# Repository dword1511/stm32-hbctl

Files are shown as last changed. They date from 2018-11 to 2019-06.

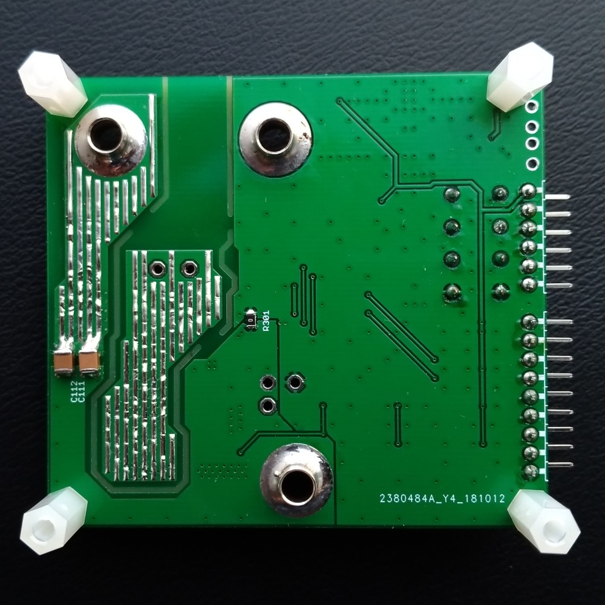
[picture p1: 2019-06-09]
pcb/pcb-photo-back.jpg

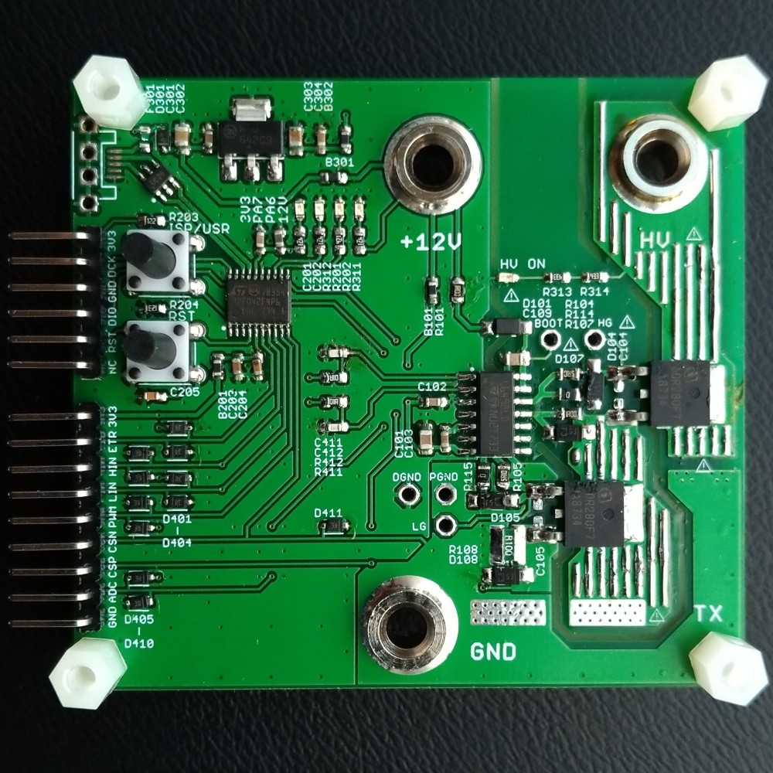
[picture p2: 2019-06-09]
pcb/pcb-photo-front.jpg

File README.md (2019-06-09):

# STM32-based half-bridge controller

This firmware code uses an `STM32F042` MCU to generate waveform for a STMicro `L6498` half-bridge driver,
which drives the MOSFETs in the inverter.

This particular inverter delivers 1 MHz AC current for our capacitive power transfer (CPT) project.
It has onboard buttons allowing us to cycle through 1 MHz +/- 100 kHz, with a few kHz of resolution.
It also has USB for ISP/DFU.

Unusual things this firmware does:

* Using HSI48 trimming in conjunction with timer prescaler to deliver a resolution of a few kHz across a large frequency range.
* Using a generic timer (rather than the advanced one) to generate complementary waveforms with dead time.

## General Build Instructions

You will need the following packages (Debian/Ubuntu):

* build-essential
* gcc-arm-none-eabi
* git
* dfu-util

The firmware can be loaded via USB DFU. However, you can also flash and debug via SWD. To do so, install the following package:

* stlink-tools
* gdb-multiarch

This project uses `libopencm3`. It will be automatically checked out during the building process.
To build the firmware, run `make`. To flash it, hold the `ISP/USR` button on the board, connect the board to USB, and then run `make flash-dfu`.

## Special Directions for CPT

Please be aware of the high voltage, especially at matching network's output.

Connect the inverter to the matching network first. Do not power on the inverter without any load.
Connect 12 V DC power to the 12 V port with a 4 mm banana test lead. Connect a variable DC power source to the HV port. Connect the ground together to GND.

Power the board on and observe the LEDs starting to flash. Use the `ISP/USR` button to enable the half-bridge. Then use the same button to cycle through frequencies.
The matching network reaches resonance when the output voltage peaks. Bridge current can be monitored by attaching an oscilloscope probe to the `CSP` pin.

## Publication

This project was part of the following work. Please kindly consider citing the paper as shown:

```
@inproceedings{Capttery,
 author = {Zhang, Chi and Kumar, Sidharth and Bharadia, Dinesh},
 title = {{Capttery: Scalable Battery-like Room-level Wireless Power}},
 booktitle = {Proc. of ACM MobiSys},
 year = {2019},
}
```

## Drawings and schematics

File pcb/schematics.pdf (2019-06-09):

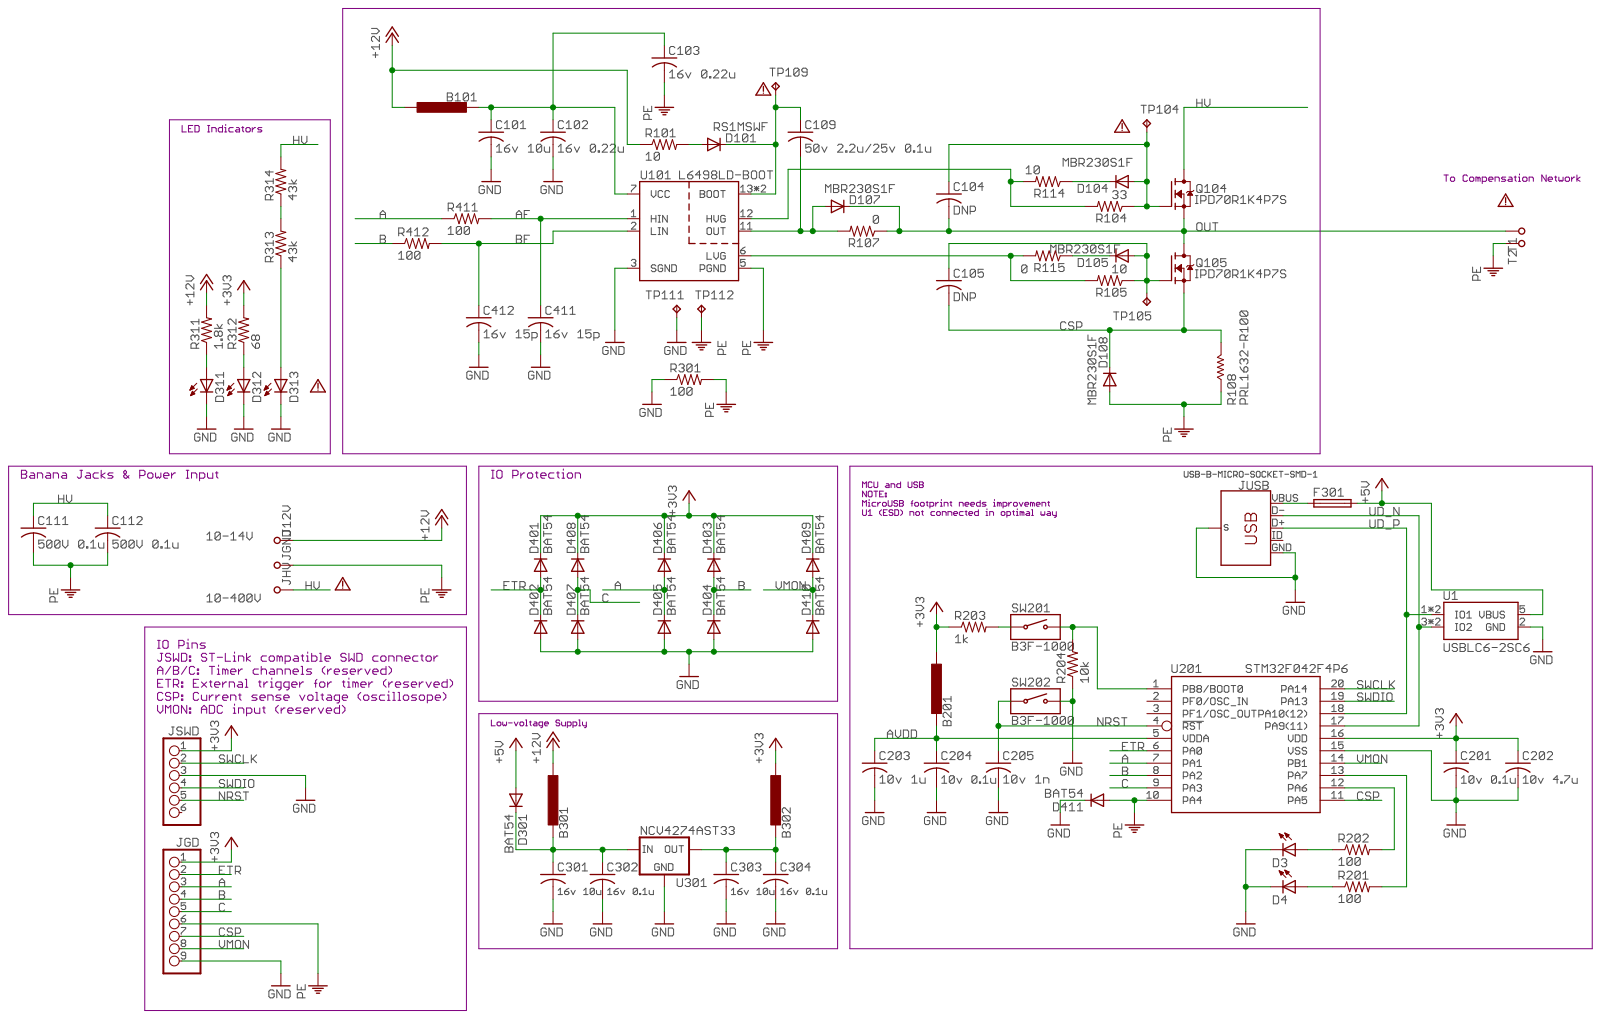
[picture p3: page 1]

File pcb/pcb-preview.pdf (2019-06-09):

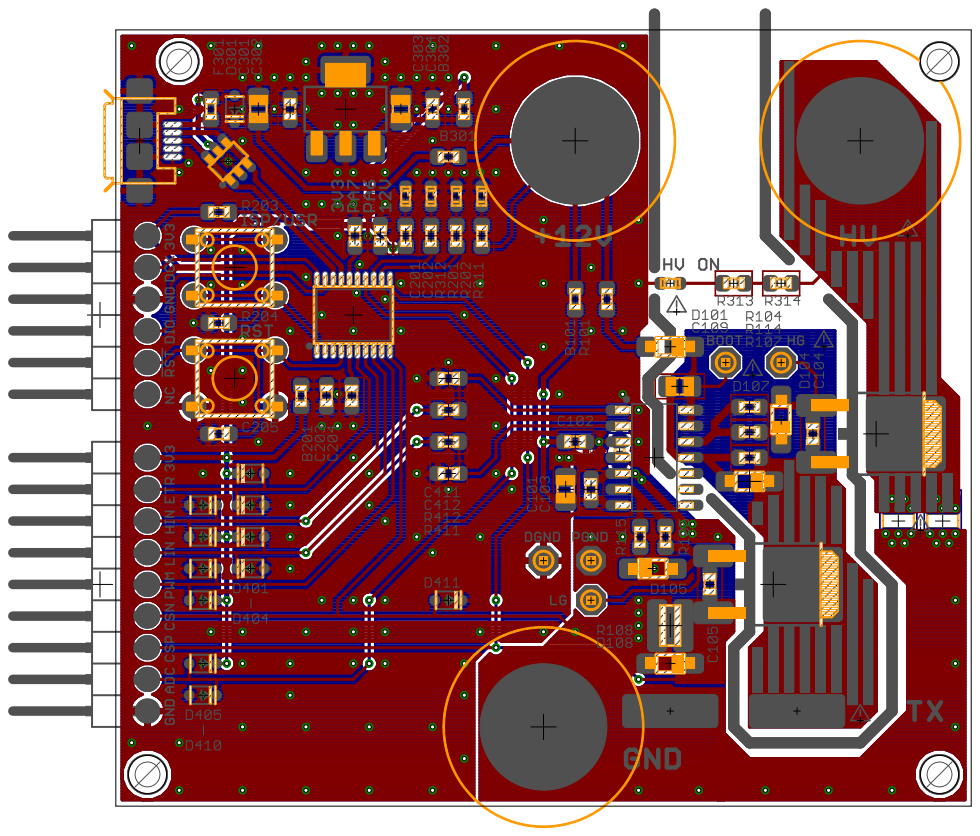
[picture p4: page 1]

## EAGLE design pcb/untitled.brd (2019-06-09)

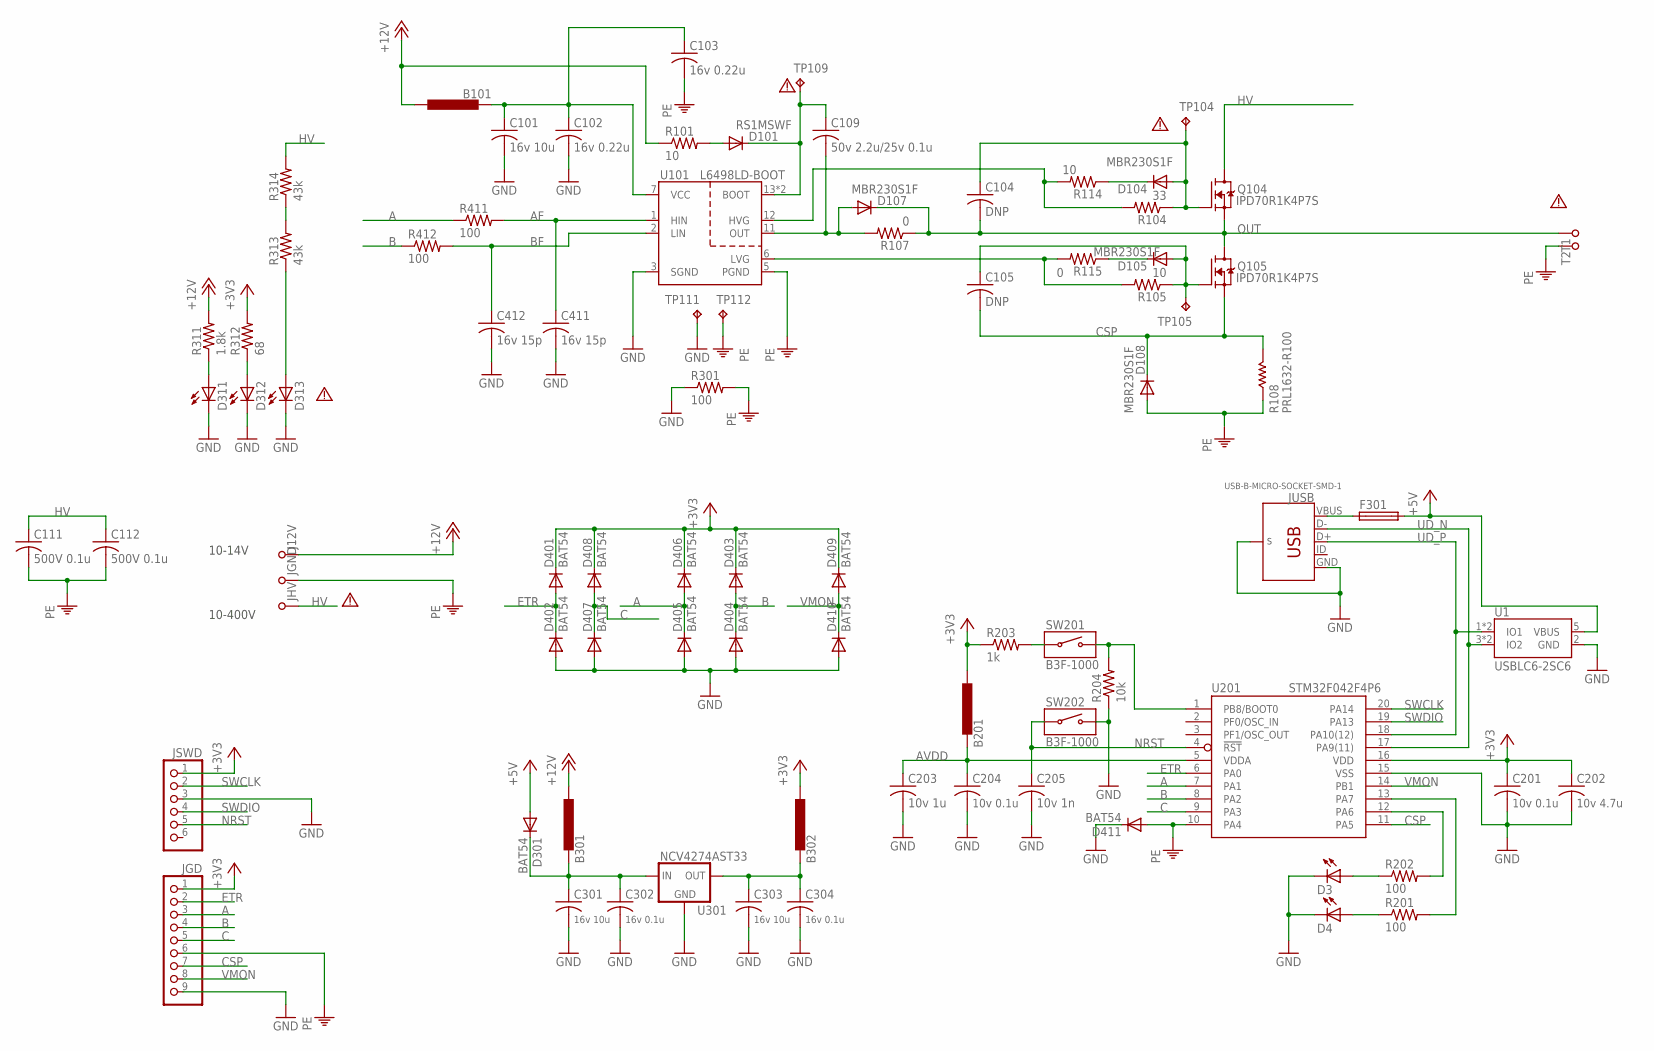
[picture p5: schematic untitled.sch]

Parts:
B101, B201, B301, B302: BEAD-0603; 0603
C101, C301, C303: 16v 10u; C0805
C102, C103: 16v 0.22u; C0603
C104, C105: DNP; C0603
C109: 50v 2.2u/25v 0.1u; C0805
C111, C112: 500V 0.1u; C1210
C201, C204: 10v 0.1u; C0603
C202: 10v 4.7u; C0603
C203: 10v 1u; C0603
C205: 10v 1n; C0603
C302, C304: 16v 0.1u; C0603
C411, C412: 16v 15p; C0603
D3, D4, D311, D312, D313: LEDSML0603; SML0603
D101: RS1MSWF; SOD123
D104, D105, D107, D108: MBR230S1F; SOD123
D301, D401, D402, D403, D404, D405, D406, D407, D408, D409, D410, D411: BAT54; SOD323-R
F301: FUSE-0603; 0603
J12V: BANANA_JACKKEYSTONE-575; KEYSTONE-575
JGD: PINHD-1X9/90; 1X09/90
JGND: BANANA_JACKKEYSTONE-575; KEYSTONE-575
JHV: BANANA_JACKKEYSTONE-575; KEYSTONE-575
JSWD: PINHD-1X6/90; 1X06/90
JUSB: USB-B-MICRO-SOCKET-SMD-1
Q104, Q105: IPD70R1K4P7S; TO-252AA
R101, R105, R114: 10; R0603
R104: 33; R0603
R107, R115: 0; R0603
R108: PRL1632-R100; 1206W
R201, R202, R301, R411, R412: 100; R0603
R203: 1k; R0603
R204: 10k; R0603
R311: 1.8k; R0603
R312: 68; R0603
R313, R314: 43k; R0603
SILK1, SILK2, SILK7, SILK11, SILK14: CAUTION-1.3MM
SW201, SW202: B3F-1000; B3F-10XX
T1, T2: TP; PAD-7.5X2.5
TP104, TP105, TP109, TP111, TP112: TPPAD1-13; P1-13
U1: USBLC6-2SC6; SOT-23-6
U101: L6498LD-BOOT; SOIC-14
U201: STM32F042F4P6; TSSOP-20
U301: NCV4274AST33; SOT-223

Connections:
+3V3: B201.2, B302.2, C201.1, C202.1, D401.C, D403.C, D406.C, D408.C, D409.C, JGD.1, JSWD.1, R203.1, R312.2, U201.16 (VDD)
+5V: D301.A, F301.2, U1.5 (VBUS)
+12V: B101.2, B301.2, J12V.P$1, R101.1, R311.2
A: D405.C, D406.A, JGD.3, R411.1, U201.7 (PA1)
AF: C411.1, R411.2, U101.1 (HIN)
AVDD: B201.1, C203.1, C204.1, U201.5 (VDDA)
B: D403.A, D404.C, JGD.4, R412.1, U201.8 (PA2)
BF: C412.1, R412.2, U101.2 (LIN)
C: D407.C, D408.A, JGD.5, U201.9 (PA3)
CSP: C105.2, D108.C, JGD.7, Q105.3 (S), R108.2, U201.11 (PA5)
ETR: D401.A, D402.C, JGD.2, U201.6 (PA0)
GND: C101.2, C102.2, C201.2, C202.2, C203.2, C204.2, C205.2, C301.2, C302.2, C303.2, C304.2, C411.2, C412.2, D3.C, D4.C, D311.C, D312.C, D313.C, D402.A, D404.A, D405.A, D407.A, D410.A, D411.C, JGD.9, JSWD.3, JUSB.GND, JUSB.MT1 (SHIELD), JUSB.MT2 (SHIELD), JUSB.P$1 (SHIELD), JUSB.P$2 (SHIELD), R204.1, R301.1, SW202.3 (B), SW202.4 (B), TP111.TP, U1.2 (GND), U101.3 (SGND), U201.15 (VSS), U301.2 (GND), U301.4 (GND)
HV: C111.1, C112.1, JHV.P$1, Q104.4 (D), R314.2
unnamed: D101.A, R101.2
unnamed: D105.C, R115.1
unnamed: R313.2, R314.1
unnamed: R105.2, R115.2, U101.6 (LVG)
unnamed: C105.1, D105.A, Q105.1 (G), R105.1, TP105.TP
unnamed: D104.C, R114.1
unnamed: R203.2, SW201.1 (COM), SW201.2 (COM)
unnamed: D3.A, R202.1
unnamed: C109.1, D101.C, TP109.TP, U101.13 (BOOT), U101.14 (BOOT)
unnamed: D4.A, R201.1
unnamed: R204.2, SW201.3 (B), SW201.4 (B), U201.1 (PB8/BOOT0)
unnamed: B301.1, C301.1, C302.1, D301.C, U301.1 (IN)
unnamed: F301.1, JUSB.VBUS
unnamed: R202.2, U201.12 (PA6)
unnamed: B302.1, C303.1, C304.1, U301.3 (OUT)
unnamed: B101.1, C101.1, C102.1, C103.1, U101.7 (VCC)
unnamed: R201.2, U201.13 (PA7)
unnamed: D313.A, R313.1
unnamed: C104.1, D104.A, Q104.1 (G), R104.1, TP104.TP
unnamed: R104.2, R114.2, U101.12 (HVG)
unnamed: C109.2, D107.A, R107.2, U101.11 (OUT)
unnamed: D312.A, R312.1
unnamed: D311.A, R311.1
NRST: C205.1, JSWD.5, SW202.1 (COM), SW202.2 (COM), U201.4 (!RST!)
OUT: C104.2, D107.C, Q104.3 (S), Q105.4 (D), R107.1, T1.1
PE: C103.2, C111.2, C112.2, D108.A, D411.A, JGD.6, JGND.P$1, R108.1, R301.2, T2.1, TP112.TP, U101.5 (PGND), U201.10 (PA4)
SWCLK: JSWD.2, U201.20 (PA14)
SWDIO: JSWD.4, U201.19 (PA13)
UD_N: JUSB.D-, U1.3 (IO2), U1.4 (IO2), U201.17 (PA9(11))
UD_P: JUSB.D+, U1.1 (IO1), U1.6 (IO1), U201.18 (PA10(12))
VMON: D409.A, D410.C, JGD.8, U201.14 (PB1)

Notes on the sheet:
10-14V
10-400V

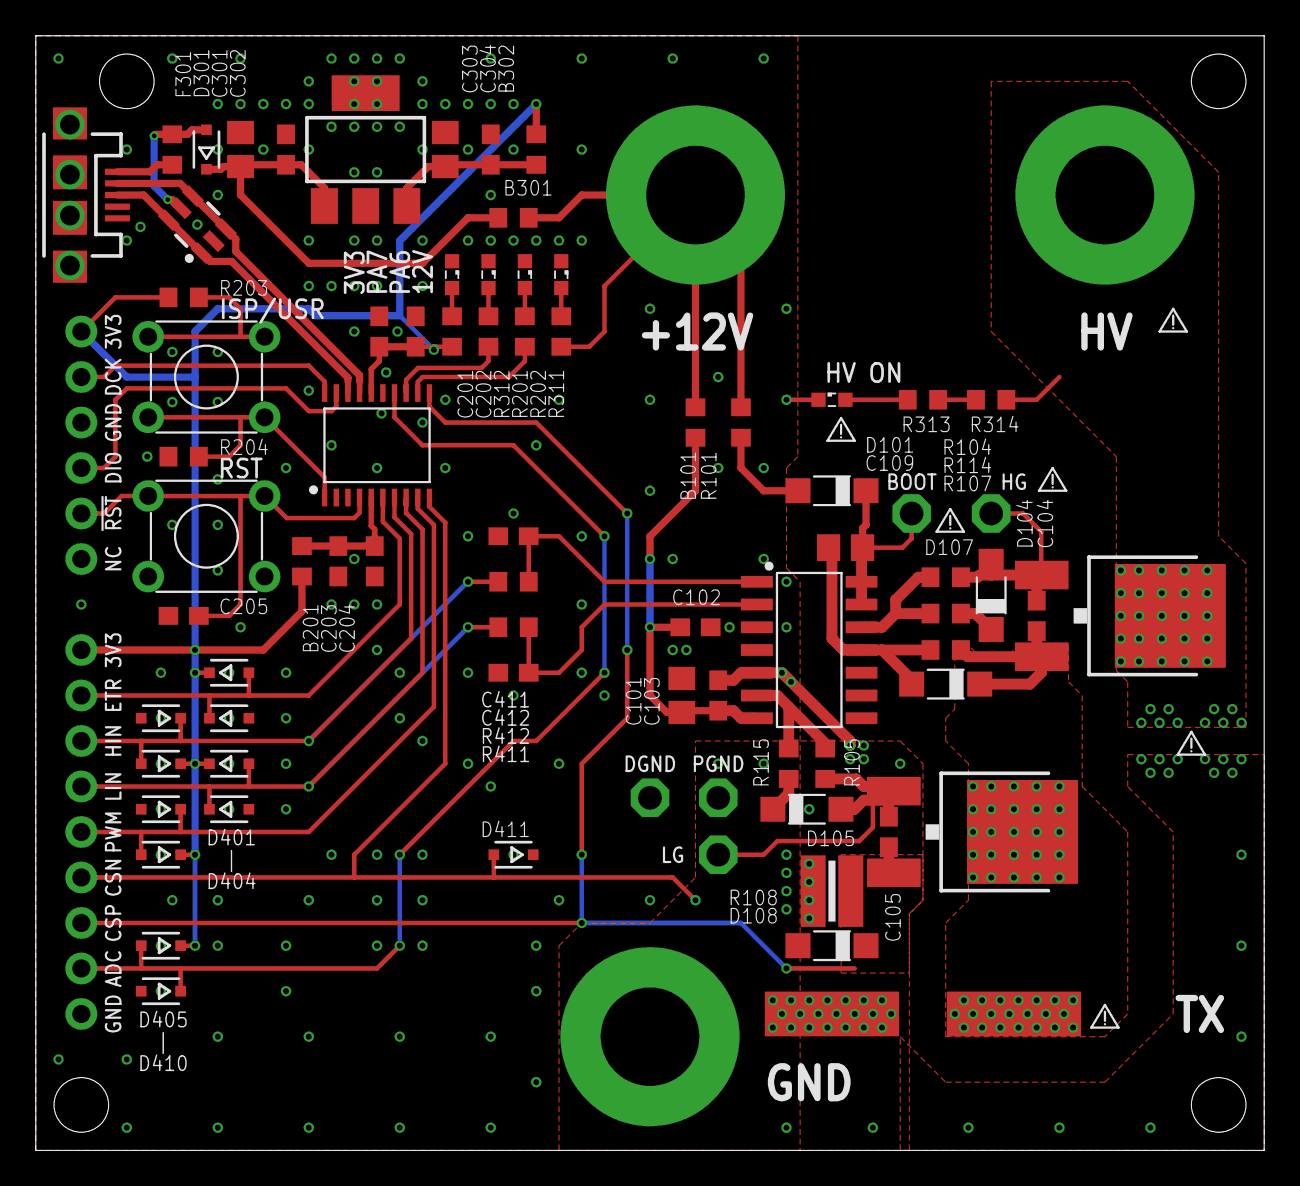
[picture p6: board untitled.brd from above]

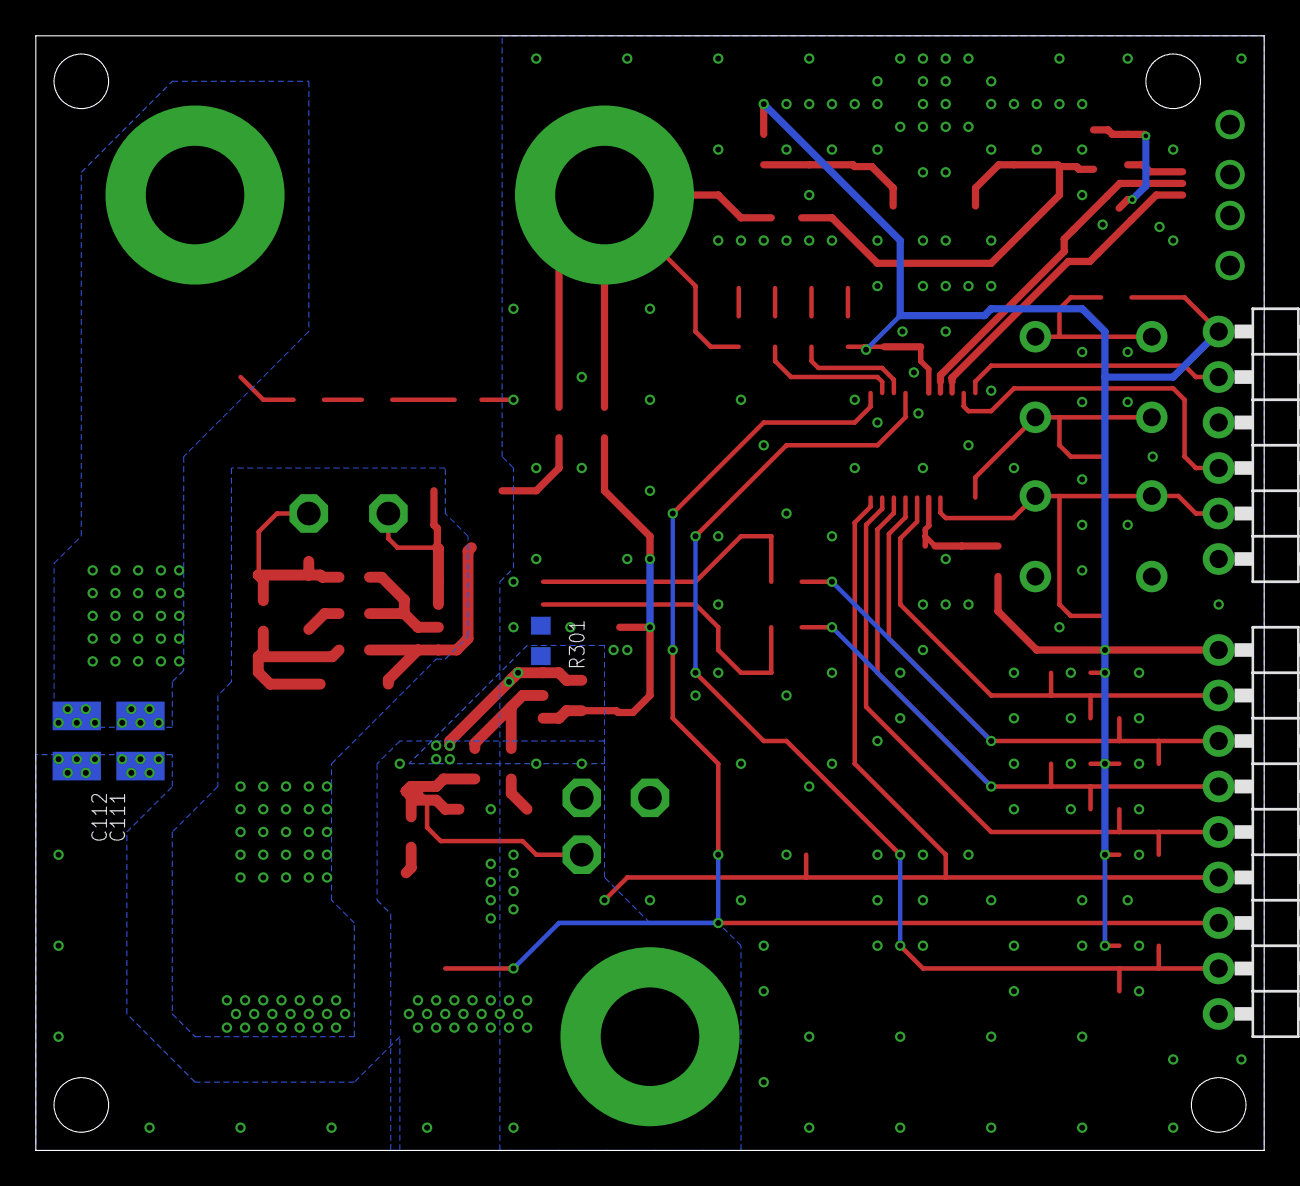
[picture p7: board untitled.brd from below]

Board: 2 copper layers, 68.6 x 62.2 mm, 91 parts (5 on the bottom side), 44 nets.

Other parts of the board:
SILK3: CAUTION-1.3MM

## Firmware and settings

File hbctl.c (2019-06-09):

#include <libopencm3/stm32/rcc.h>
#include <libopencm3/stm32/gpio.h>

#include "bsp.h"
#include "cs.h"
#include "pwm.h"
#include "tick.h"
#include "hsi48trim.h"


#define TICK_PERIOD_MS  10
#define CS_SAMP_T_MS    5 /* Must be smaller than tick interval */
#define OVP_MA          1000
#define F_NOM           950000
#define F_TOL           50000
#define F_TOL_COARSE    100000
#define F_MAX           (F_NOM + F_TOL)
#define F_MIN           (F_NOM - F_TOL)
#define DUTY            127 /* out of 255. Use 127 or less for soft switching */
#define DEAD_TIME       50
#define DELAY_LONG_MS   500
#define DELAY_SHORT_MS  50


/* Exceptions */
static void halt(void) {
  uint32_t i;

  while (true) {
    for (i = 0; i < 10000000; i ++) {
      asm("nop\n");
    }
    gpio_toggle(GPIO_PORT_LED, HCI_LED_ALL);
  }
}

void nmi_handler(void)
__attribute__ ((alias ("halt")));

void hard_fault_handler(void)
__attribute__ ((alias ("halt")));


/* HCI */
static void delay_a_bit(void) {
  uint32_t i;

  for (i = 0; i < 3000000; i ++) {
    asm("nop\n");
  }
}

static void hci_setup(void) {
  gpio_mode_setup(GPIO_PORT_BUT, GPIO_MODE_INPUT, GPIO_PUPD_NONE, GPIO_PIN_BUT);

  gpio_set_output_options(GPIO_PORT_LED, GPIO_OTYPE_PP, GPIO_OSPEED_2MHZ, HCI_LED_ALL);
  gpio_mode_setup(GPIO_PORT_LED, GPIO_MODE_OUTPUT, GPIO_PUPD_NONE, HCI_LED_ALL);

  delay_a_bit(); /* System tick unavailable yet */
  gpio_set(GPIO_PORT_LED, HCI_LED_ALL);
  delay_a_bit();
  gpio_clear(GPIO_PORT_LED, HCI_LED_ALL);
  delay_a_bit();
  delay_a_bit();
  gpio_set(GPIO_PORT_LED, HCI_LED_ALIVE);
}

static void wait_button(void) {
  uint32_t i = 0;

  while (!gpio_get(GPIO_PORT_BUT, GPIO_PIN_BUT)) {
    asm("wfi");
  }

  /* De-bounce TODO: use tick */
  for (i = 0; i < 30000; i ++) {
    if (gpio_get(GPIO_PORT_BUT, GPIO_PIN_BUT)) {
      i = 0;
    }
  }
}

/* OVP */

void tick_routine_cb(void) {
  /* Over current protection */
  if (cs_measure_ma() > OVP_MA) {
    pwm_disable();
  }

  tick_routine_confirm_done();
}


int main(void) {
  uint32_t reset_reason = RCC_CSR & RCC_CSR_RESET_FLAGS;
  RCC_CSR |= RCC_CSR_RMVF; /* Clear reset flags */

  /* HSI48 does not need to be piped through PLL and can be tuned on-the-fly safely */
  rcc_clock_setup_in_hsi48_out_48mhz();

  /* Enable & reset GPIOA and GPIOB */
  rcc_periph_clock_enable(RCC_GPIOA);
  rcc_periph_reset_pulse(RST_GPIOA);
  gpio_mode_setup(GPIOA, GPIO_MODE_ANALOG, GPIO_PUPD_PULLDOWN, GPIO_ALL & (~(GPIO13 | GPIO14))); /* Keep SWD active, pull down all pins to keep bridge disabled */
  rcc_periph_clock_enable(RCC_GPIOB);
  rcc_periph_reset_pulse(RST_GPIOB);
  gpio_mode_setup(GPIOB, GPIO_MODE_ANALOG, GPIO_PUPD_PULLDOWN, GPIO_ALL);

  hci_setup();

  hsi48trim_setup();
  cs_setup(CS_SAMP_T_MS);
  pwm_setup();
  tick_setup(TICK_PERIOD_MS);

  /* In case of EMI (all GPIO setup done) */
  gpio_port_config_lock(GPIOA, GPIO_ALL);
  gpio_port_config_lock(GPIOB, GPIO_ALL);

  if (reset_reason & (RCC_CSR_WWDGRSTF | RCC_CSR_IWDGRSTF)) {
    /* Notify WDG reset */
    while (true) {
      tick_delay_ms(DELAY_SHORT_MS);
      gpio_toggle(GPIO_PORT_LED, HCI_LED_ALL);
    }
  }

  {
    uint32_t freq = F_MIN;

    while (true) {
      wait_button();

      if (!gpio_get(GPIO_PORT_LED, HCI_LED_RUN)) {
        /* Bridge has been disabled due to POR or OVP, (re)enable per user request */
        pwm_config(freq, DUTY, DEAD_TIME);
      } else {
        pwm_disable();
        tick_delay_ms(DELAY_SHORT_MS);

#if F_TOL_COARSE >= F_TOL
        /* Fine-grained adjustment */
        if (hsi48trim_goto_next() == 0) {
          /* HSI48 trimming has gone through one round, do coarse adjustment */
          freq = pwm_get_next_freq();
          if (freq > F_MAX) {
            freq = F_MIN;
          }
          pwm_config(freq, DUTY, DEAD_TIME);
          freq = pwm_get_next_freq();
	  if (freq > F_MAX) {
            freq = F_MIN;
          }
	  pwm_config(freq, DUTY, DEAD_TIME);
        } else {
          /* Fine adjustment has been done */
          pwm_enable();
        }
#else
        /* Coarse-grained adjustment */
        freq = pwm_get_next_freq();
        if (freq > F_MAX) {
          freq = F_MIN;
        }
	pwm_config(freq, DUTY, DEAD_TIME);
#endif
      }
    }
  }

  return 0;
}

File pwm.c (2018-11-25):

/* Complementary PWM with deadtime using GP Timer (instead of Advanced TIM1) */
/* Implemented with center-aligned counter and 2 PWM channels in different modes */
/* NOTE: this further limits freq resolution... */

#include <libopencm3/cm3/assert.h>

#include <libopencm3/stm32/rcc.h>
#include <libopencm3/stm32/gpio.h>
#include <libopencm3/stm32/timer.h>


#include "bsp.h"
#include "pwm.h"


#define TO_TIM_SCALE(T, tr) (((uint32_t)(tr)) * (T) / 255)


//TODO: sync (use ETR to reset counter...)
void pwm_setup(void) {
  gpio_set_output_options(GPIO_PORT_PWM, GPIO_OTYPE_PP, GPIO_OSPEED_100MHZ, GPIO_PIN_HI | GPIO_PIN_LO);
  gpio_set_af(GPIO_PORT_PWM, GPIO_AF2, GPIO_PIN_SYNC | GPIO_PIN_HI | GPIO_PIN_LO);
  gpio_mode_setup(GPIO_PORT_PWM, GPIO_MODE_AF, GPIO_PUPD_NONE, GPIO_PIN_HI | GPIO_PIN_LO);
  gpio_mode_setup(GPIO_PORT_PWM, GPIO_MODE_AF, GPIO_PUPD_PULLDOWN, GPIO_PIN_SYNC);

  rcc_periph_clock_enable(PWM_TIM_RCC);
  rcc_periph_reset_pulse(PWM_TIM_RST);

  timer_disable_oc_output(PWM_TIM, TIM_OC1);
  timer_disable_oc_output(PWM_TIM, TIM_OC2);
  timer_disable_oc_output(PWM_TIM, TIM_OC3);
  timer_disable_oc_output(PWM_TIM, TIM_OC4);

  timer_set_mode(PWM_TIM, TIM_CR1_CKD_CK_INT, TIM_CR1_CMS_CENTER_1, TIM_CR1_DIR_UP);
  timer_set_prescaler(PWM_TIM, 0);
  timer_continuous_mode(PWM_TIM);

  timer_disable_oc_clear(PWM_TIM, PWM_OC_HI);
  timer_enable_oc_preload(PWM_TIM, PWM_OC_HI);
  timer_set_oc_mode(PWM_TIM, PWM_OC_HI, TIM_OCM_PWM1); /* Active when TIMx_CNT < TIMx_CCR1 */
  timer_disable_oc_clear(PWM_TIM, PWM_OC_LO);
  timer_enable_oc_preload(PWM_TIM, PWM_OC_LO);
  timer_set_oc_mode(PWM_TIM, PWM_OC_LO, TIM_OCM_PWM2); /* Active when TIMx_CNT >= TIMx_CCR1 */

  pwm_disable();
  /* Output should always be active (otherwise GPIO becomes high-Z) */
  timer_enable_counter(PWM_TIM);
  timer_enable_oc_output(PWM_TIM, PWM_OC_LO);
  timer_enable_oc_output(PWM_TIM, PWM_OC_HI);
}

/* freq in Hz, duty/deadtime in 0 - 255 */
void pwm_config(uint32_t freq, uint8_t duty, uint8_t deadtime) {
  uint16_t period = rcc_apb1_frequency / (freq * 2) - 1;
  uint16_t ocv_hi = TO_TIM_SCALE(period, duty - deadtime / 2);
  uint16_t ocv_lo = TO_TIM_SCALE(period, 255 - duty + deadtime / 2);

  pwm_disable(); /* Avoid shoot-through */

  cm3_assert(duty + deadtime <= 255);
  cm3_assert(ocv_lo > ocv_hi); /* Low-side's OCV has to be greater than high-side's. Will not hold if deadtime is 0. */

  timer_set_period(PWM_TIM, period);
  timer_set_counter(PWM_TIM, 0);
  timer_set_oc_value(PWM_TIM, PWM_OC_HI, ocv_hi);
  timer_set_oc_value(PWM_TIM, PWM_OC_LO, ocv_lo);

  pwm_enable();
}

uint32_t pwm_get_next_freq(void) {
  uint16_t next_period = TIM_ARR(PWM_TIM) - 1;

  return rcc_apb1_frequency / ((next_period + 1) * 2);
}

void pwm_enable(void) {
  gpio_set(GPIO_PORT_LED, HCI_LED_RUN);

  /* Must be in this sequence to avoid shoot-through */
  timer_set_oc_mode(PWM_TIM, PWM_OC_LO, TIM_OCM_PWM2);
  timer_set_oc_mode(PWM_TIM, PWM_OC_HI, TIM_OCM_PWM1);
}

void pwm_disable(void) {
  /* Must be in this sequence to avoid shoot-through */
  timer_set_oc_mode(PWM_TIM, PWM_OC_HI, TIM_OCM_INACTIVE);
  timer_set_oc_mode(PWM_TIM, PWM_OC_LO, TIM_OCM_ACTIVE);

  gpio_clear(GPIO_PORT_LED, HCI_LED_RUN);
}

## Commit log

2018-08-07 add debug, fix adc init, add freq limit
    [hbctl.c]
2018-11-24 bugfixes, some bug left
    [hbctl.c]
2019-06-09 add pcb and doc
    [untitled.brd, untitled.sch]
